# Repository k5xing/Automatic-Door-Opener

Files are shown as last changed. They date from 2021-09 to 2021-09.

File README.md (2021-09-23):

# Automatic-Door-Opener
Lab Projects Developed in ECE298

This project automates an entry/exit doorway to a customer site that senses customers automatically with programmable trigger levels for proximity. There are four labs to finish the project. The work done in each lab is described below and in the reports. Some detailed information of this project can be seen on Page 8 of [project overview.pdf](https://github.com/k5xing/Project-Overview/blob/main/project%20overview%20-%20Kehan%20Xing.pdf), and the code programmed in Lab3 is in [STM32_Workspace/Lab3/Core/Src/main.c](https://github.com/k5xing/Automatic-Door-Opener/blob/main/Lab3%20%20-%20Prototype%20Phase%201/STM32_Workspace/Lab3/Core/Src/main.c).

### Lab1 - Feasibility Model Phase 1
	• Design and pick sensors, actuators, and user I/O the project requires
	• Implement component tests in Proteus 

### Lab2 - Feasibility Model Phase 2
	• Design voltage translation interfacing

### Lab3 - Prototype Phase 1
	• Upgrade design to include all component models and connections
	• Program embedded MCU code and test functionalities

### Lab4 - Prototype Phase 2
	• Design a Printed Circuit Board (PCB) Layout

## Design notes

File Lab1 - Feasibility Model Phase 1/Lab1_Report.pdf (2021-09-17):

# Lab 1 – Feasibility Model Phase 1

ECE 298 – S2021

Team Members Kehan Xing (k5xing@uwaterloo.ca) Yiru Wu (y645wu@uwaterloo.ca)

Team Number 50

## Part 1 – Project Design Requirements

### 1. Functional Requirements

A. Automatically open the doorway to 8 feet wide when detecting a customer
B. Stop the door movement within 0.2 seconds after the collision switch is closed
C. Limit the door speed to 0.5 ft/sec when the collision switch opens again until the door is closed

### 2. Non-functional Requirements

A. Safety: The automatic door needs to ensure the safety of users during use.
B. Power efficiency: The automatic door needs to ensure the power effect and reduces losses.
C. Durability: The automatic door needs to guarantee the quality of use within a certain period of time.

### 3. Constraint Requirements

A. Maximum cost of $150 to develop the project
B. Maximum weight of 2 kg for the hardware components
C. Maximum PCB size of 9cm x 15cm

## Part 2 – Project Considerations for I/O

### Project Sensors and User Inputs

- Outside/inside Distance Proximity Sensor: The sensor will react to the trigger and

output the reaction pulse signal, we could use an opamp to scale the sensor reaction

pulse signal into the MCU digital input range.

- Door Position Limit Switches(2): The output of the switch can be regarded as the

presence or absence of current, so we could use a signal converter to transform the

current into a voltage range for the MCU, and then use the internal ADC to get the

digital input.

- Motor Sensor: The motor sensor will output continuous digital signals, so we could

use an opamp to scale the pulse signal output into the MCU digital input range.

- Collision Switch: The output of the switch can be regarded as the presence or

absence of current, so we could use a signal converter to transform the current into

a voltage range for the MCU, and then use the internal ADC to get the digital input

- Keypad: The pins on the MCU will receive a voltage input when a key is pressed, so

we use an opamp to scale the keypad output voltage to the MCU input pin voltage

range, and then use the ADC to convert the input to digital input.

### Project Actuators and User Outputs

- LCD Display: Use MCU’s parallel interface to input signals to display characters.
- LED (4): Use a transistor so the MCU can switch the high-current device on and off.
- Door Motor: Use the internal PWM to control the motor
- Motor Controller IC: Use the MCU’s serial interface to control a motor controller IC.

### Project MCU Internal Resources

a. Internal Resources
- ADC: The ADC will be used to convert Analog input to Digital input. For example, the

input we receive from a switch will be a voltage of 0V or 3.3V, and the ADC will

convert it to 0 or 1.

- Interrupt: The motor needs to be stopped once the collision switch or the door

position limit switch is closed, and that requires an interrupt module to handle.

- GPIO: As we listed above, there are many user inputs and outputs as well as sensors

and actuators in this project. They need GPIO functions to read or write.

- Timer: With the timer and the motor sensor, we can calculate the speed and the

acceleration of the motor.

- PWM: Pulse-width modulation is needed to control the motor.
b. Software parameters
- Duration: We need a parameter to read the timer and use it to calculate speed and

acceleration.

- Conversion factor: There could be many conversion factors, such as conversion

between different distance units.

- Sensor status: We need parameters to read sensor status and use the signals we

receive to control the motor.

- Motorcycle: There should be a counter to track how many cycles the motor has

spinned in order to calculate the distance.

- Keypad input: Keypad inputs including selected mode and parameters in the setup

mode need software parameters to read them.

## Part 3 – Device Testing Methodology

### Device 1 – ECE_GEN_PBUTTON (Switch)

We chose this pushbutton switch to represent the Door Position Limit switches and the Collision Switch. To test the switch, a 3.3V input voltage and a voltage scope are used. One end of the switch is connected to the input voltage, and the other end is connected to the scope. We expect to see the scope show 3.3V when the switch is closed and show 0V when it’s open. The schematic in Figures 1&2 with a pull-down resistor R shows our idea.

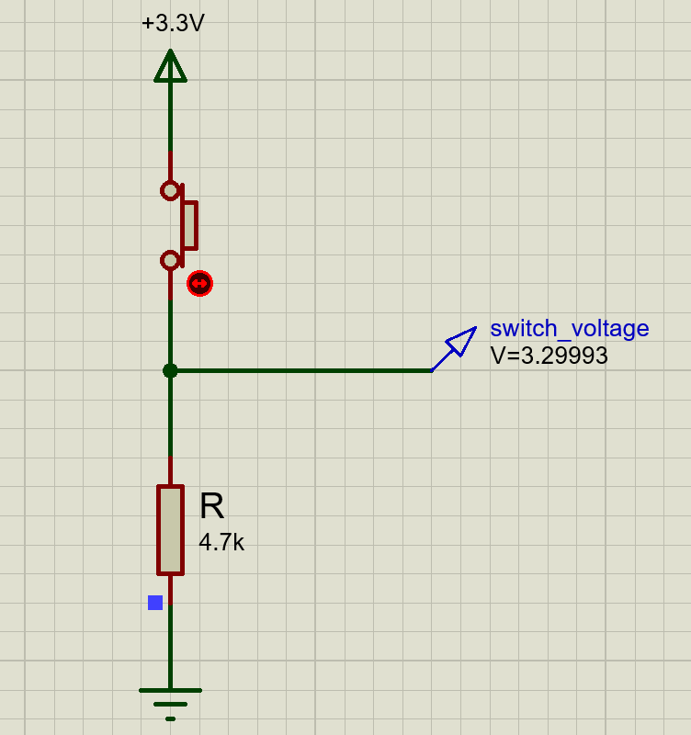
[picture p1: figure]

Figure 1: The schematic of ECE_GEN_PBUTTON -- Switch closed

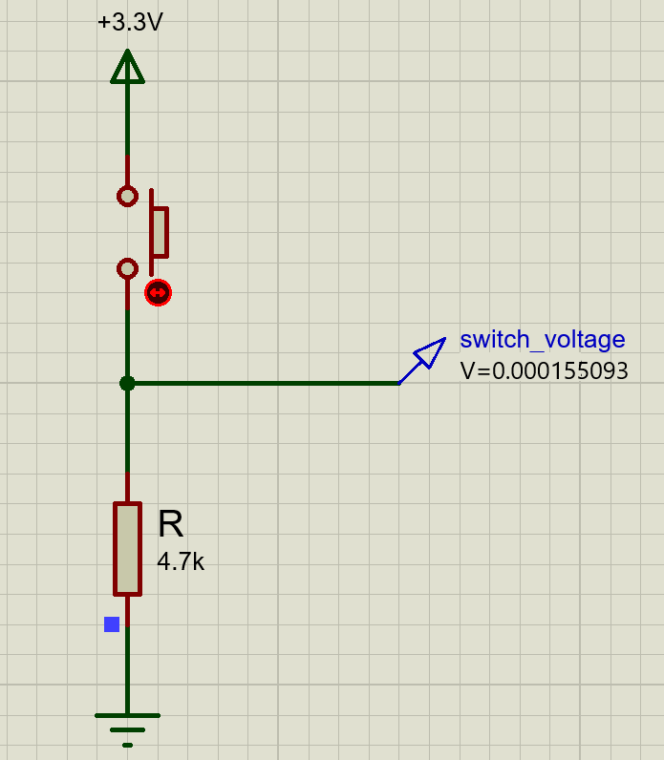
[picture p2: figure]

Figure 2: The schematic of ECE_GEN_PBUTTON -- Switch open

Verification: The switch works as expected. When the switch is closed, the voltage scope named switch_voltage shows a voltage value very close to 3.3V. Also, when the switch is open, the voltage scope shows a value close to 0V. This means the logic level is high when the switch is closed and is low when the switch is open.

Validation: As claimed in the verification section, a voltage of 5V indicates a high logic level, and a voltage of 0V indicates a low logic level. When using the switch in our project, we want the voltage scope to be replaced by an input pin on the MCU. In this case, the pin will read a high state when the switch is closed and a low state when the switch is open with the internal ADC, so this will work properly in our project.

### Device 2 – HCSR04 (Distance Proximity Sensor)

This ultrasonic ranging module is chosen for the Outside/Inside Distance Proximity Sensors. To test this sensor, we used a pulse voltage for its trigger input and an oscilloscope to show the trigger input and receive the echo pulse output. We expect to see both the signals on the oscilloscope.

Figure 3 and Figure 4 show the schematic and the signal displayed by the oscilloscope with distance = 50cm, and Figure 5 and 6 show those with distance = 200cm.

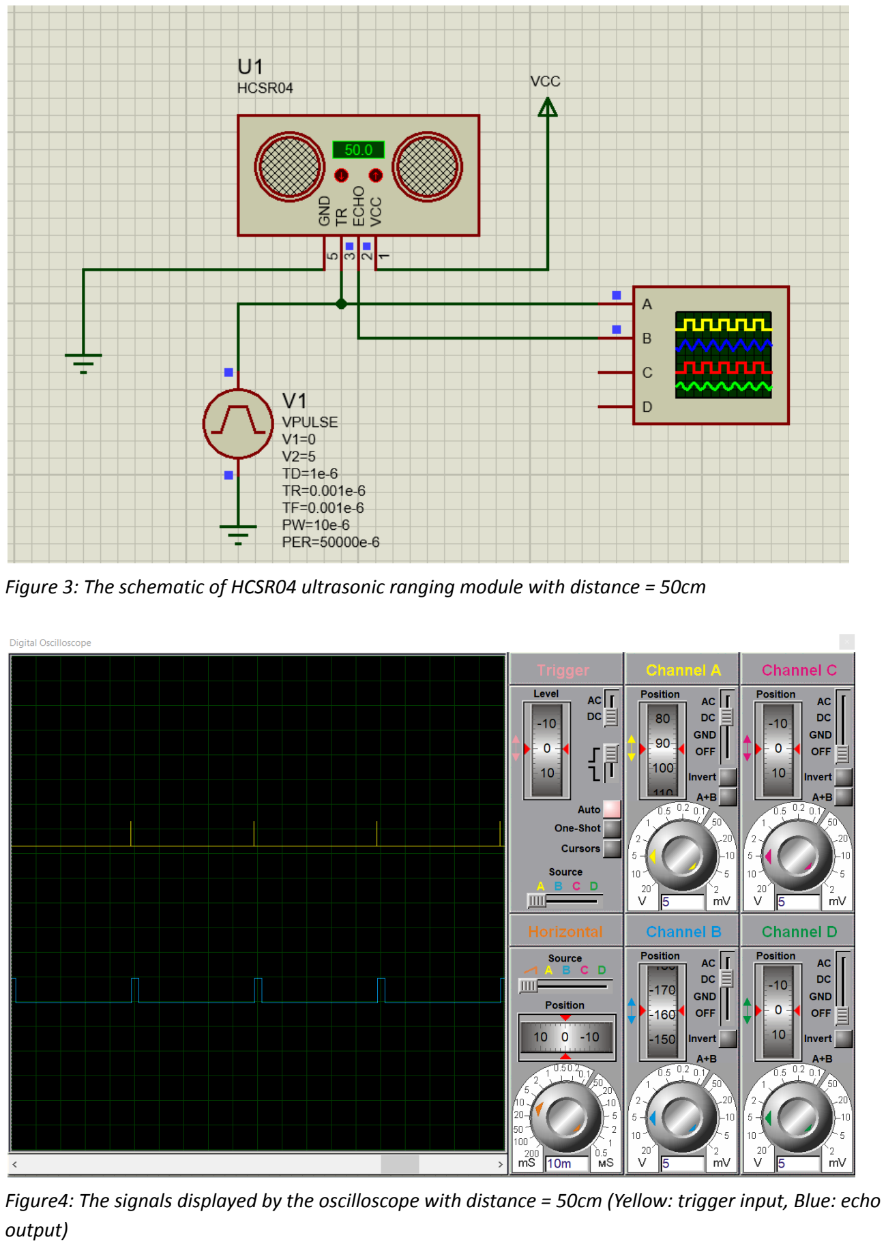
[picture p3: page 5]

Figure 3: The schematic of HCSR04 ultrasonic ranging module with distance = 50cm

Figure4: The signals displayed by the oscilloscope with distance = 50cm (Yellow: trigger input, Blue: echo output)

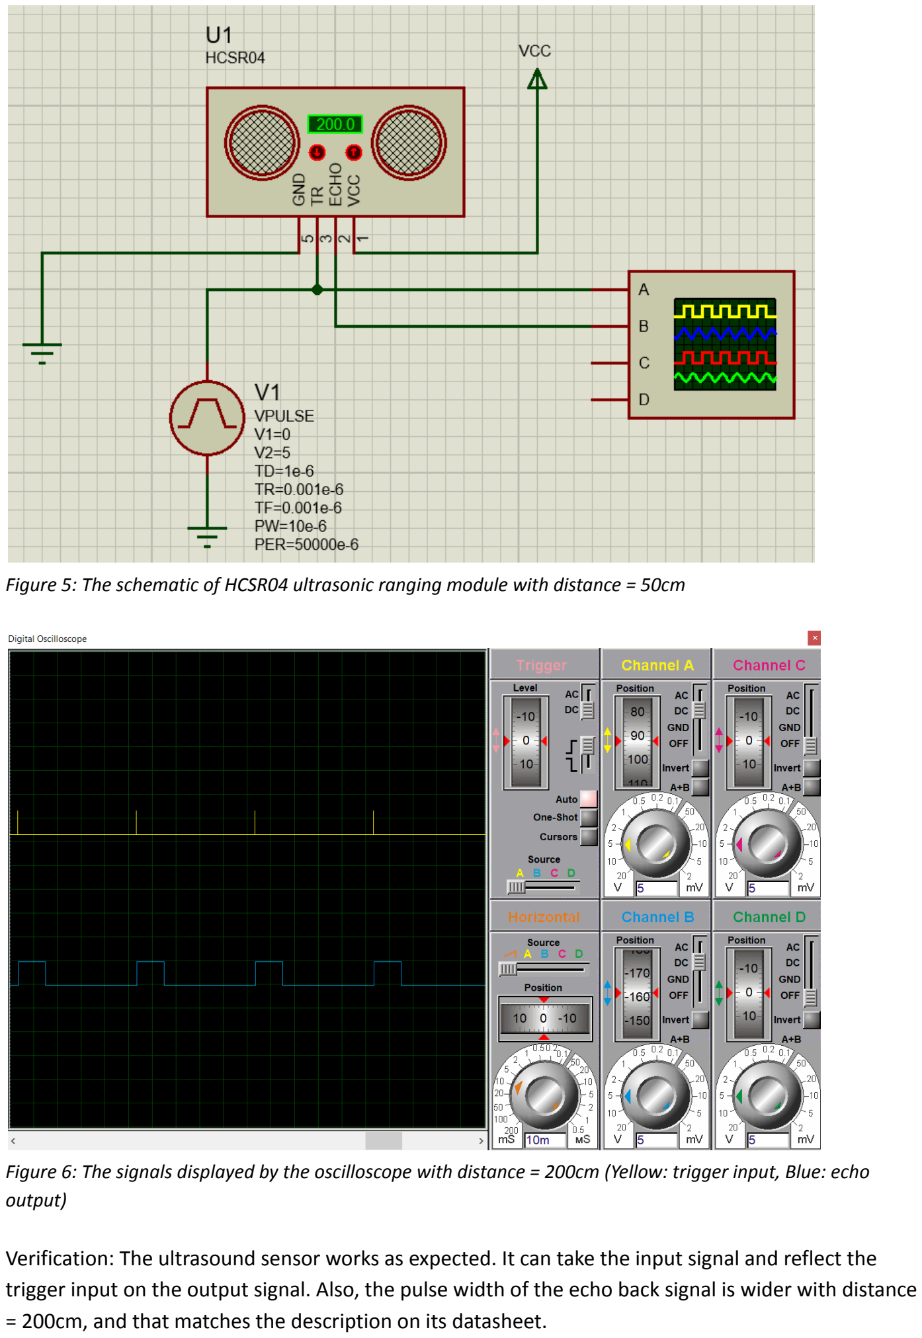
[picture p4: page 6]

Figure 5: The schematic of HCSR04 ultrasonic ranging module with distance = 50cm

Figure 6: The signals displayed by the oscilloscope with distance = 200cm (Yellow: trigger input, Blue: echo output)

Verification: The ultrasound sensor works as expected. It can take the input signal and reflect the trigger input on the output signal. Also, the pulse width of the echo back signal is wider with distance = 200cm, and that matches the description on its datasheet.

Validation: The ultrasonic sensor is used to measure the distance of a target object by emitting ultrasonic sound waves, and converts the reflected sound into an electrical signal. This is exactly the functionality we want for the distance proximity sensor. Also, the detecting range of this ultrasonic ranging module is 2cm - 500cm, and the required range of our project is 60cm - 240cm. Therefore, this ultrasonic sensor can be used in our project.

### Device 3 – KEYPAD - PHONE (Keypad)

The keypad - phone is chosen to be used in Setup Mode. To test this keypad, we selected four DC power supplies each providing different voltage. Then using three DC voltmeters to test the voltage changes when the keys were pushed. Figure 7, figure 8, figure 9 and figure 10 show the schematic and the voltage change.

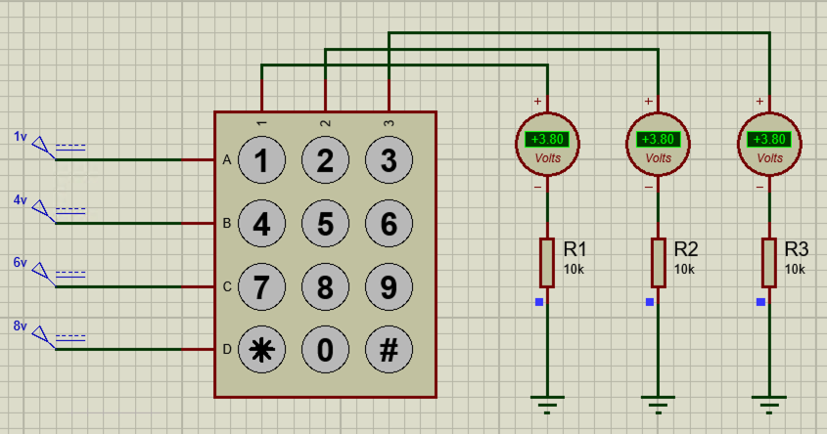
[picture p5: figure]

Figure 7: The schematic of KEYPAD module (initial state)

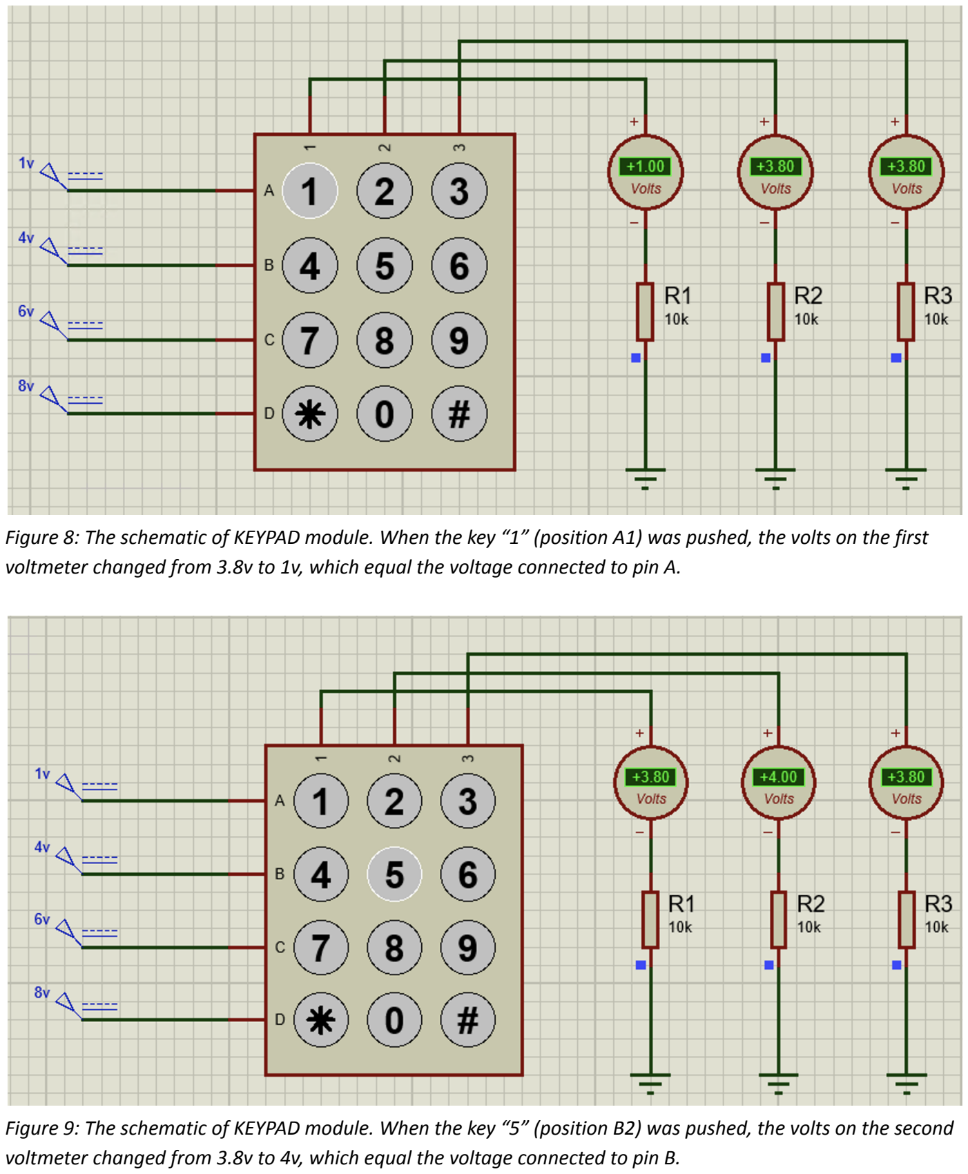
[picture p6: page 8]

Figure 8: The schematic of KEYPAD module. When the key “1” (position A1) was pushed, the volts on the first voltmeter changed from 3.8v to 1v, which equal the voltage connected to pin A.

Figure 9: The schematic of KEYPAD module. When the key “5” (position B2) was pushed, the volts on the second voltmeter changed from 3.8v to 4v, which equal the voltage connected to pin B.

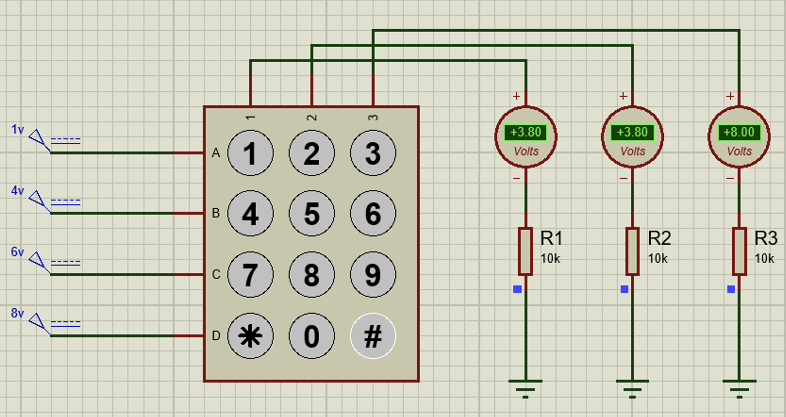
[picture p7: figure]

Figure 10: The schematic of KEYPAD module. When the key “#” (position D3) was pushed, the volts on the third voltmeter changed from 3.8v to 8v, which equal the voltage connected to pin D.

Verification: The keypad works as expected. When the key located at (x,y) be pressed, the pin x and the pin y are connected, so the voltage of pin y equals the voltage of pin x, as measured by voltmeter. Detailed information of all the cases is described under the figures.

Validation: When using the keypad in our project, the total 7 pins of the keypad will be connected to the MCU. Then we could detect which key is pressed by checking which pins are connected. Also, the user input required in our project are just numbers, so this keypad can satisfy the requirement.

### Device 4 – ECE298_FAST_DCMOTOR_ENCODER (Motor/Motor Sensor)

This model is chosen to be used as motor and motor sensors. To test this motor, we need a DC voltage to supply the power and an oscilloscope to show the digital signal detected from the motor. Figure 11, figure 12 and figure 13 show the schematic and the signal displayed by the oscilloscope using a pulse voltage input. Figure 14, figure 15 and figure 16 shows that using a DC voltage.

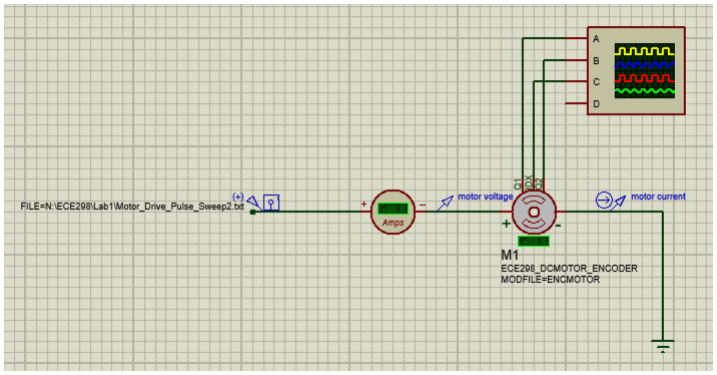
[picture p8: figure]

Figure 11: The schematic of ECE298_FAST_DCMOTOR_ENCODER using pulse voltage

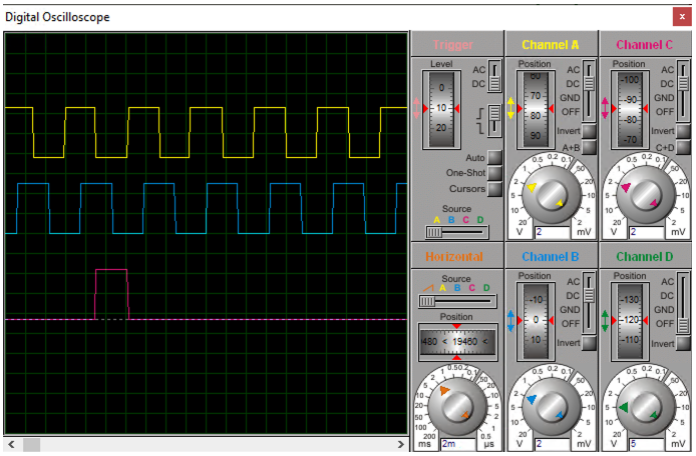
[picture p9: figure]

Figure 12: The signals output displayed by the oscilloscope using pulse voltage(Yellow: Q1, Blue: Q2, Red: IDX)

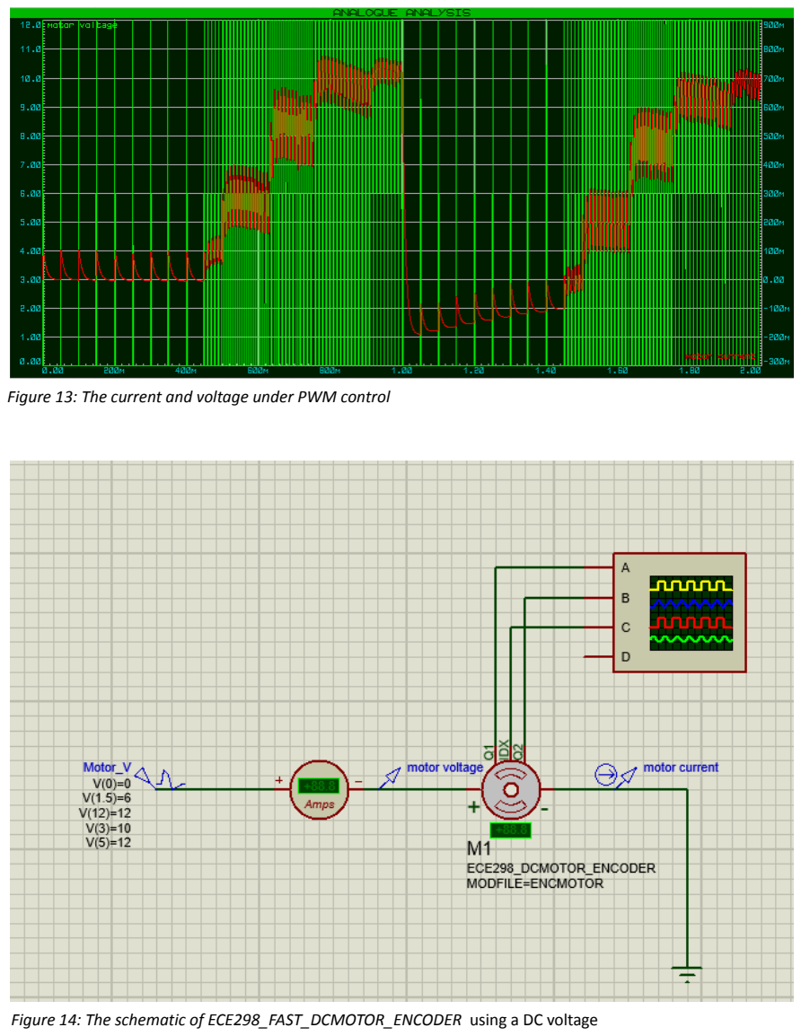
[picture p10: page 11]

Figure 13: The current and voltage under PWM control

Figure 14: The schematic of ECE298_FAST_DCMOTOR_ENCODER using a DC voltage

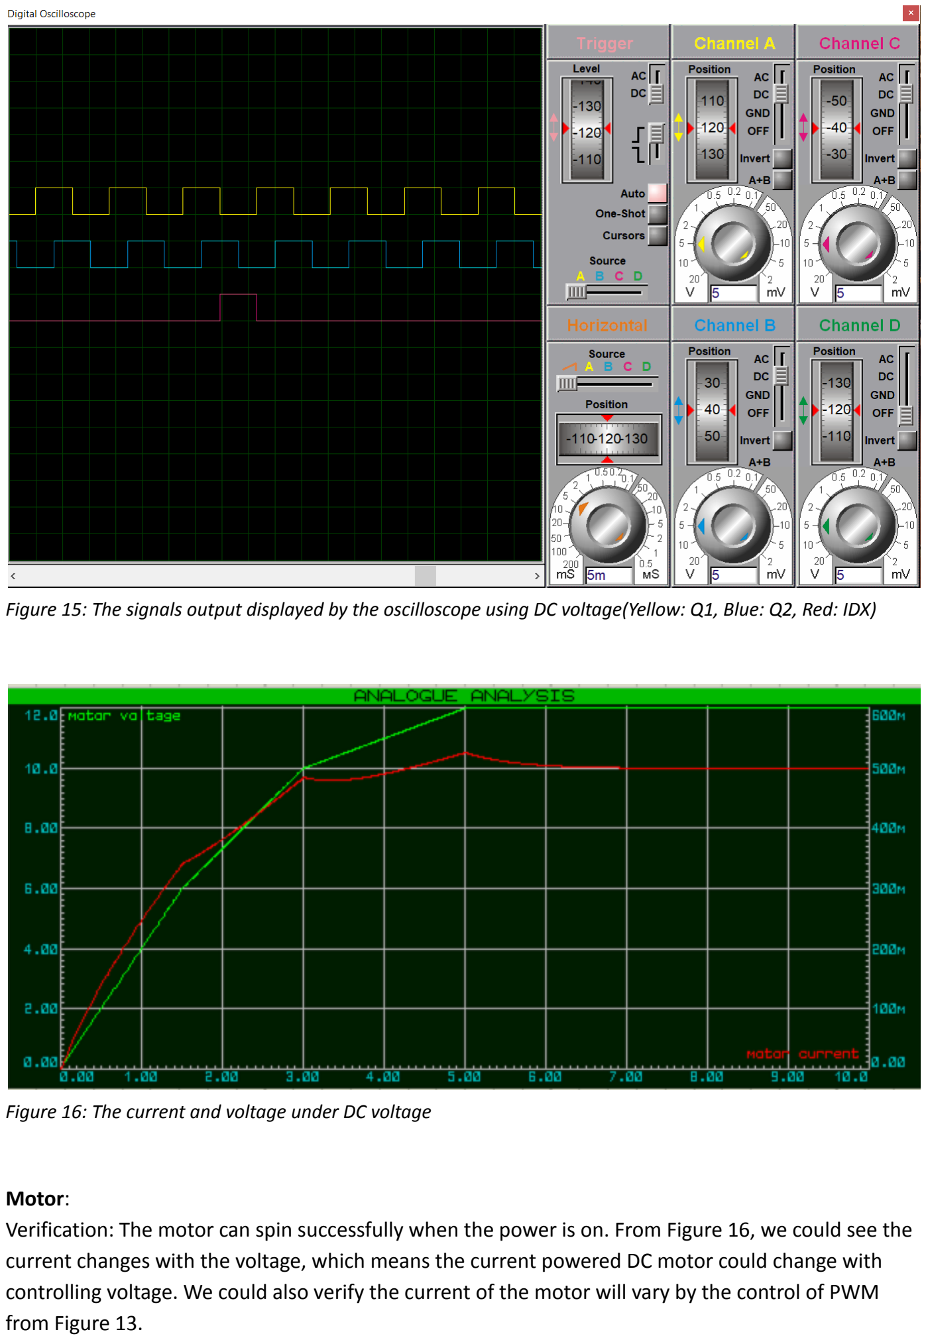
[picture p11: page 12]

Figure 15: The signals output displayed by the oscilloscope using DC voltage(Yellow: Q1, Blue: Q2, Red: IDX)

Figure 16: The current and voltage under DC voltage

Motor:
Verification: The motor can spin successfully when the power is on. From Figure 16, we could see the current changes with the voltage, which means the current powered DC motor could change with controlling voltage. We could also verify the current of the motor will vary by the control of PWM from Figure 13.

Validation: This motor is a good choice for us because it has a sensor attached. It can also spin properly. In the project, we are able to change the speed of the motor by controlling the PWM and make the motor rotate in the opposite direction by reversing power.

Motor Sensor:
Verification: From the graph generated by the oscilloscope, we could see the digital signals from the pins of the motor, so the motor sensor is working properly to record the move of the sensor.

Validation: In the project, we could use the digital signals from Q1 and Q2 to determine the direction of the motor. Also, we could use an internal counter to record the number of edges of the digital signal as revolutions of the motor.

### Device 5 – LED (LED)

Three kinds of LEDs are used in this project, and we decided to use animated LED models with different colors to represent them. These LEDs have a forward voltage of 1.95V(red), 2V(yellow) and 2.1V(green) according to the information on Piazza. And they all have a full drive current of 10mA, so we calculated the resistances of their current limiting resistors based on those values and MCU voltage of 3.3V and created a schematic.

R =

V−V
led
I
led

The schematic also used a potentiometer to change the current flows through the LEDs. After changing the LED model type to analog, the brightness of the LEDs should change with the current. The figures below show the brightness with current of approximately 100%, 50% and 20% of the full drive current.

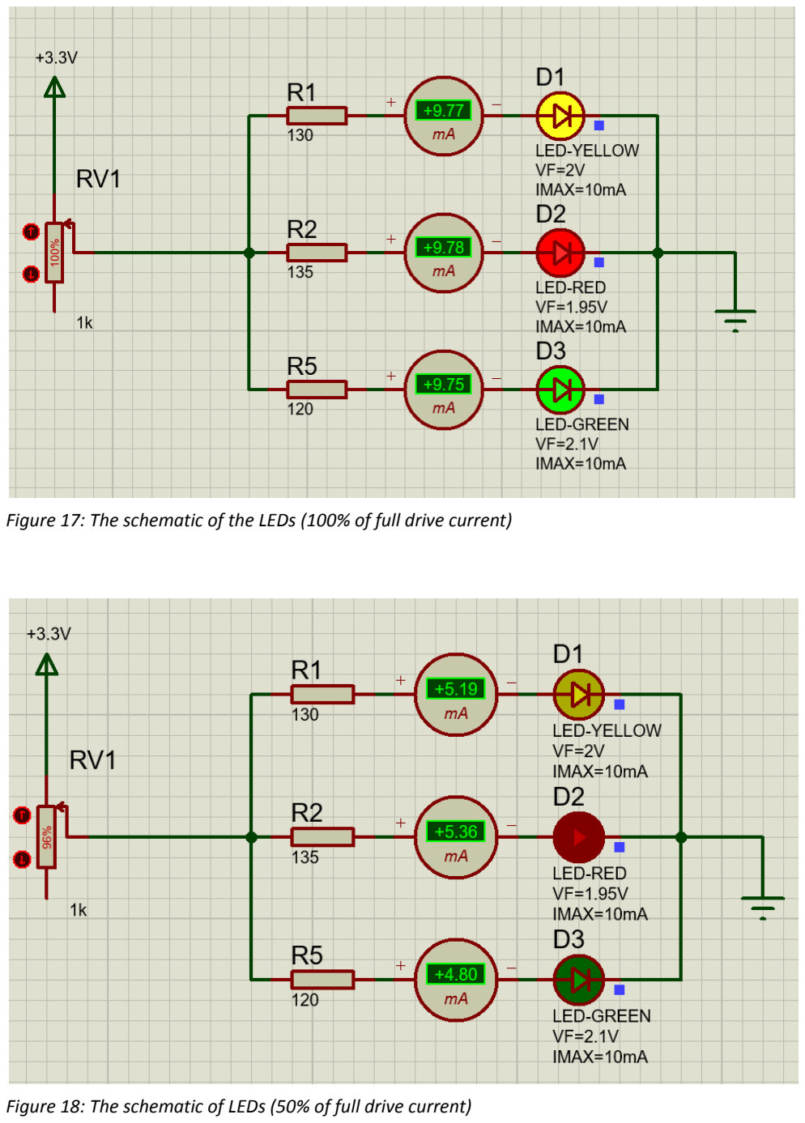
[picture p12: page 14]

Figure 17: The schematic of the LEDs (100% of full drive current)

Figure 18: The schematic of LEDs (50% of full drive current)

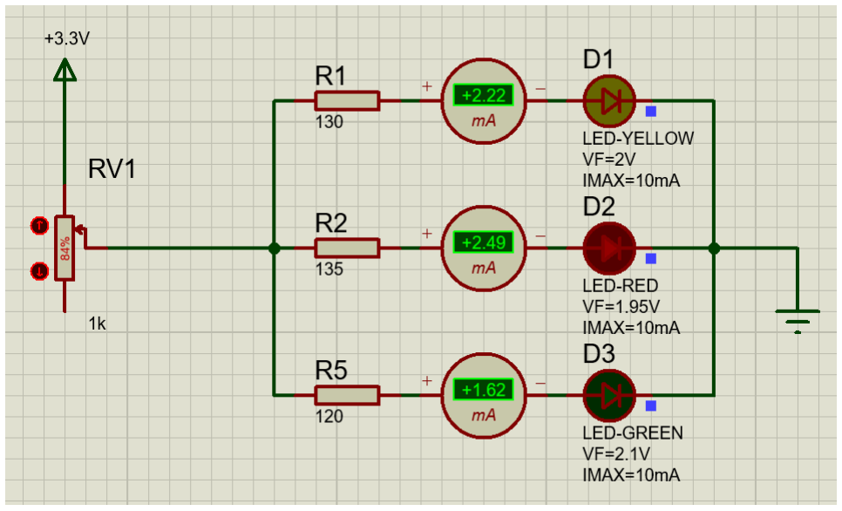
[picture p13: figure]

Figure 19: The schematic of LEDs (20% of full drive current)

Verification: The LEDs worked as expected. They can be turned on after powering the circuit, and the brightness of the LEDs changes with the current flow through them. We also confirmed the current-limiting resistors for these LEDs are calculated correctly because the ammeter displayed a value very close to 10mA when the potentiometer is not used in Figure 16.

Validation: These LEDs have a forward voltage of 1.95V, 2V and 2.1V, and our voltage source in this project will be 3.3V, so the LEDs can perform normally as shown above. For the project requirements, we only require a LED to turn on when a specific event happens. This can be achieved by addressing a high state to the pin to power the LED.

### Device 6 – LM016L– (LCD display)

We chose this LCD for our project because it is simple to use and can display letters as well as numbers. To test this device, we connect the pattern generator to the LCD like Figure 20, and change the pattern to display our group number.

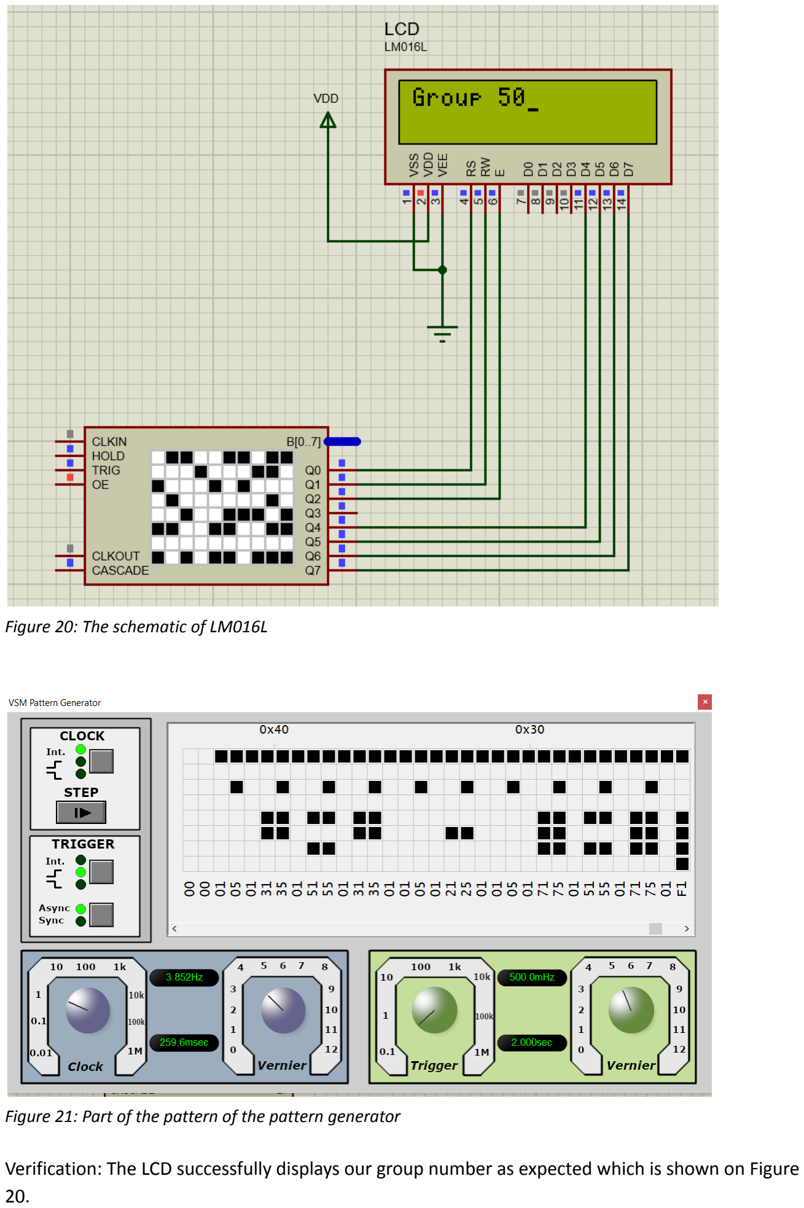
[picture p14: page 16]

Figure 20: The schematic of LM016L

Figure 21: Part of the pattern of the pattern generator

Verification: The LCD successfully displays our group number as expected which is shown on Figure 20.

Validation: In our project, we want to display mode, parameter name and parameter value. They will be either letters or numbers. We tested that both of them can be displayed successfully on this LCD, so we can use the LCD in our project.

## Part 4 – System-Level Design

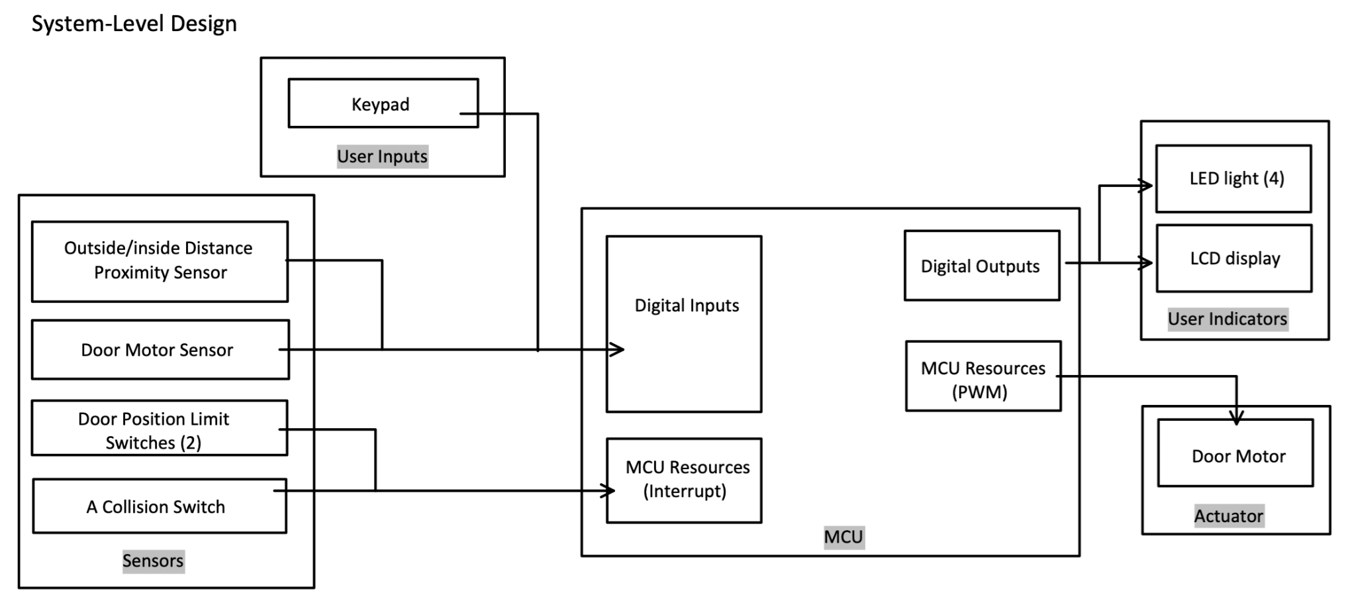
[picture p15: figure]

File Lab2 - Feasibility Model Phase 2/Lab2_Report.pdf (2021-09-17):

# Lab 2 – Feasibility Model Phase 2

ECE 298 – S2021
Lab Section: | Group: | 50

## {Switch}

### Summary

Item | Description

Purpose

A switch is required to represent the collision switch and the door position limit switches, so it will stop the door movement when a collision occurs, or the door reaches its limit position.
Device physical domain and range | The physical domain and range are not applied to this device.
Device type chosen | The chosen switch is an on/off type.
Proteus Library component name | There is no direct Proteus push button component directly
available, so ECE_GEN_PBUTTON is used in its place.
Device input / output properties | The device outputs a digital output. The type of the digital
output is push/pull, but it requires a pull-down resistor.
Device input / output range | The input/out range is not applied to this device.
MCU connectivity details | The device will connect to an MCU digital input.
Device/MCU interfacing details | There is no interface provided for the switch because it can be
connected to a 3.3V power directly.

### Schematics and Simulations


Figure 2.1.1 The schematic of ECE_GEN_PBUTTON -- Switch closed

Lab 2 – Feasibility Model Phase 2


ECE 298 S2021 | Page 2 of 13

Figure 2.1.2: The schematic of ECE_GEN_PBUTTON -- Switch open

The schematic used for the switch is same as Lab1 because the switch can connect to a 3.3V power directly without voltage translation. The switch_voltage probe represents an MCU digital input. The probe shows 3.3V when the switch is closed and shows 0V when it is open.

## {Distance Proximity Sensor}

### Summary

Item | Description
Purpose | The distance proximity sensors are required to detect people
| and objects near the door from both directions.
Device physical domain and range | The distance range that the chosen distance proximity sensor
| support is 2cm - 500cm.
Device type chosen | The chosen distance sensor is an ultrasonic ranging module.
Proteus Library component name | HCSR04
Device input / output properties | The device receives a digital input as trigger signal and outputs
| the echo back signal which is a digital output.
Device input / output range | The device requires a digital active-high trigger signal and
| outputs a variable pulse width echo signal. The recommended
| cycle period is less than 50ms, and the echo pulse width is
| proportional to the measured distance. Other information such
| as maximum/minimum pulse width and VOH/ VOL / VIH / VIL is not
| available.
MCU connectivity details | The device uses an MCU digital output for the trigger input, and
| an MCU digital input for the echo signal.
Device/MCU interfacing details | The interfaces used are digital-to-digital. The first interface
| translates the 3.3V digital input from the MCU to a 5V digital
| input and pass it to trigger signal. The second interface translate
| the 5V digital output from the echo signal translate to a 3.3V
| digital output and pass it to an MCU digital input pin.

### Schematics and Simulations

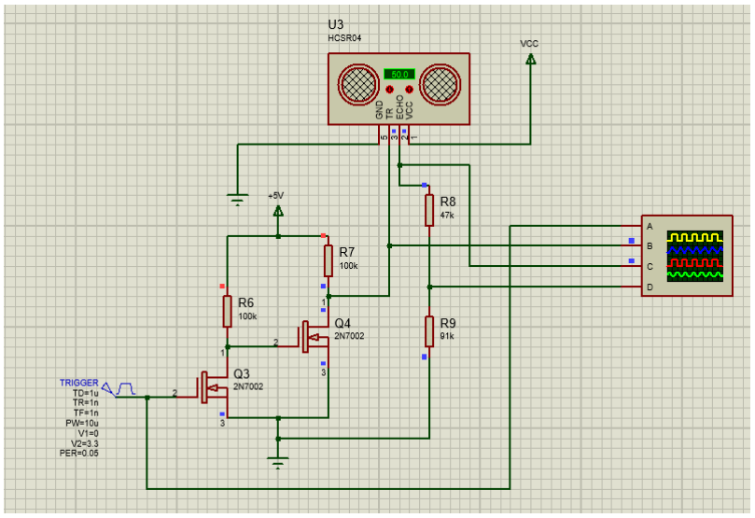
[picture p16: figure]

Figure 2.2.1: The schematic of HCSR04 ultrasonic ranging module with distance = 50cm

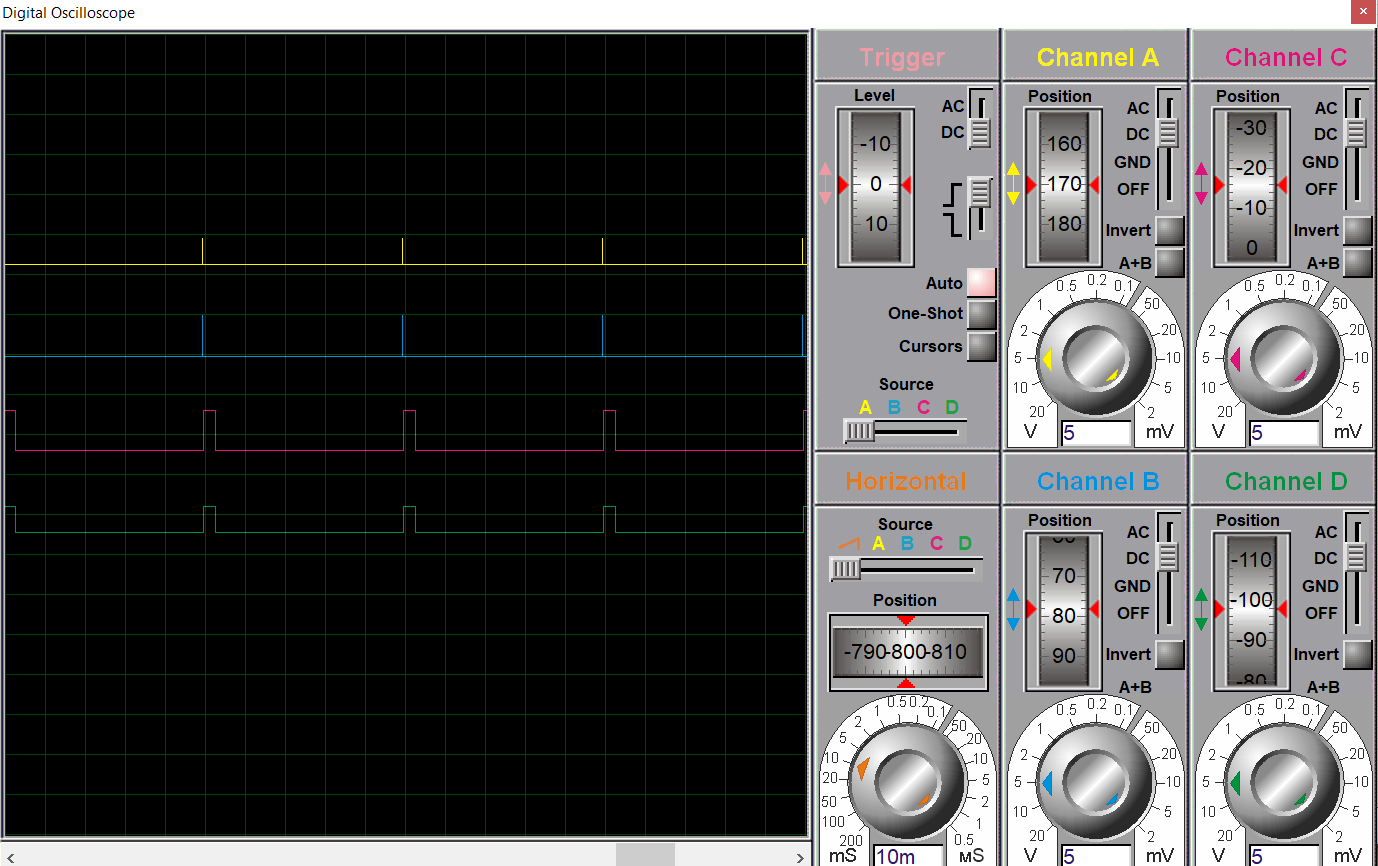
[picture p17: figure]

Figure 2.2.2 The signals displayed by the oscilloscope with distance = 50cm (Yellow: original MCU input, Blue: trigger input after translation, Pink: original echo output, Green: echo output after translation)

As described in the summary table, a step-up interface and a step-down interface are used in the schematic. The step-up interface uses two N-FET and translates the 3.3V digital input from the MCU to a 5V digital input and pass it to trigger signal. Channel A of the oscilloscope shows the original 3.3V input from MCU, and channel B shows the digital input after translation. The step-down interface uses two resistors with resistance 47k and 91k and translates the 5V digital output from the echo signal translate to a 3.3V digital output. Channel C shows the 5V digital output, and Channel D shows the signal after translation. The signal displayed in Channel D is the output that will be passed to an MCU digital input.

## {Keypad}

### Summary

Item | Description
Purpose | A keypad is required to select mode of operation and input
| parameter values.
Device physical domain and range | The keypad is an array of switches, so the physical domain and
| range are not applied to it.
Device type chosen | The keypad is an array of switches, and the switches are on/off
| type. When a key is pressed, the corresponding switch is closed;
| when a key is not pressed, the corresponding switch is open.
Proteus Library component name | KEYPAD - PHONE
Device input / output properties | The device receives three digital inputs for pins representing
| columns and outputs four digital outputs from pins representing
| rows. The type of the digital output is push/pull, but it requires
| a pull-down resistor.
Device input / output range | The keypad is an array of switches, so the input/out range is not
| applied to this device.
MCU connectivity details | The device uses three MCU digital outputs connecting to pins
| representing columns and four MCU digital inputs for pins
| representing rows.
Device/MCU interfacing details | The keypad is an array of switches, so there is no interface
| provided for the switch because it can be connected to a 3.3V
| digital signal directly.

### Schematics and Simulations

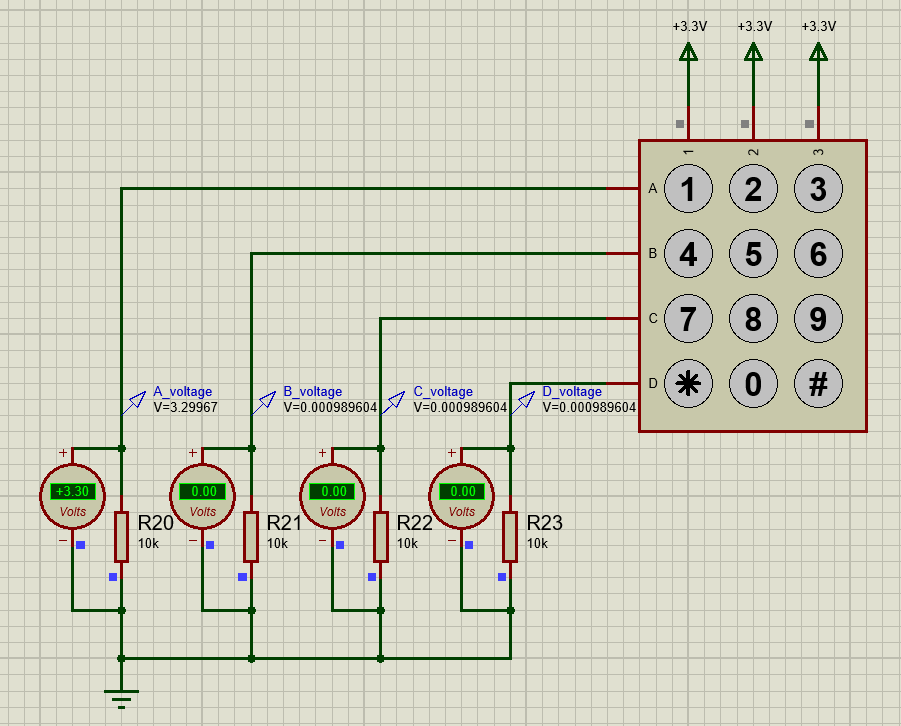
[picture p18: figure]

Figure 2.3.1: The schematic of KEYPAD_PHONE when key ‘1’ is pressed

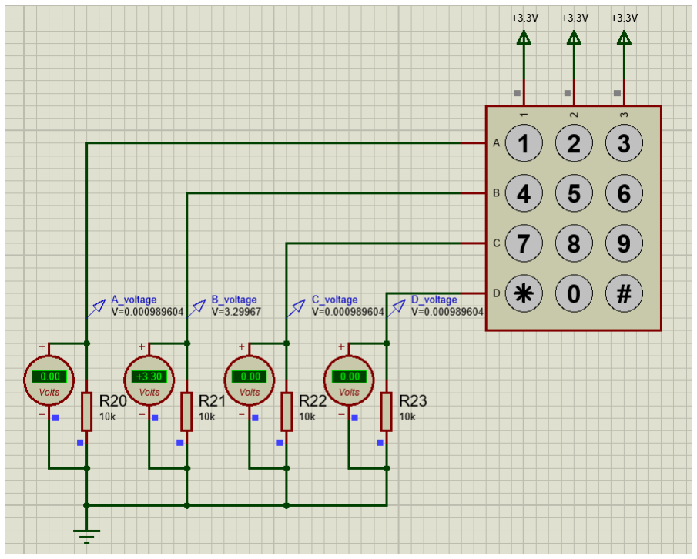
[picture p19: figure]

Figure 2.3.2: The schematic of KEYPAD_PHONE when key ‘5’ is pressed

The keypad doesn’t require voltage translations because it’s simply an array of switches. The two figures above show the schematic when the key ‘1’ and ‘5’ is pressed, and it shows that the voltage of the corresponding pin turns to 3.3V when the key is pressed. The 3.3 voltage power represents the digital signal of ‘1’ receiving from MCU digital output, and the probes labeled A_voltage, B_voltage, C_voltage, D_voltage represent the signal will be passed to MCU digital inputs.

## {LED}

### Summary

Item | Description
Purpose | Different color of LEDs are used to indicate different status of
| door motor.
Device physical domain and range | LED’s maximum brightness will depend on the specific LED.
Device type chosen | Normal LED
Proteus Library component name | LED-RED, LED_GREEN, LED_YELLOW
Device input / output properties | The device will receive the digital signal from MCU as digital
| input.
Device input / output range | We setup the current through LED to be 10mA.
MCU connectivity details | The LED will use an MCU digital output for the trigger signal.
Device/MCU interfacing details | The interface is digital to digital, if MCU inputs a ‘1’ (3.3v), the
| circuit of LED will connect to 5v voltage source and groud to
| generate a 10mA current for LED to work, the LED will light up;
| if MCU inputs a ‘0’ (0v), the LED will not light up.

### Schematics and Simulations

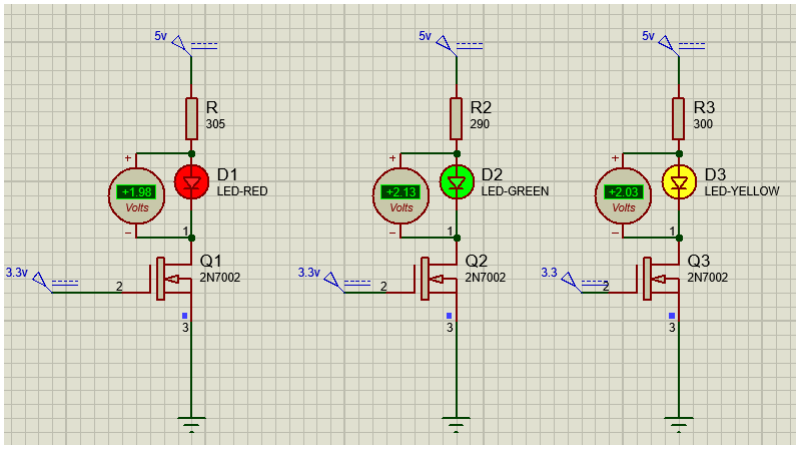
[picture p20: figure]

Figure 2.4: Schematics of converting digital input to voltage range for LEDs. To step up the voltage to the input range of LED, we add a N-FET. The #1 pin connects to the 5v and LED, #2 pin connects to the digital output of MCU, and #3 connects to ground. When MCU outputs a ‘0’, which means that V2 = 0v and V23 = 0v, then circuit between #1 pin and #3 pin is open circuit, the led would not work well. When MCU outputs a ‘1’, which means that V2=3.3v and V23=3.3v, then #1 pin and #3 pin is connected, and there is a 10mA current through the LED to support.

Through the Lab1 piazza, we knew that LEDs with different colors have different work voltage: 1.95v for red LED, 2v for yellow LED, and 2.1v for green LEDs. The current for LEDs to work is 10mA. The resistance connect to LED should be 5v-V(work)/I(work). Therefore, the resistance for red LED is 305 ohm, for yellow LED is 300 ohm, and for green LED is 290 ohm.

## {LCD}

### Summary

Item | Description
Purpose | LCD is used to indicate the Mode, Parameter Name and
| Parameter Value in Setup Mode, and it is also used to display
| the status of the automatic door.
Device physical domain and range | Operating temperature should be 0 – 50 degrees.
Device type chosen | A character display LCD
Proteus Library component name | LM016L
Device input / output properties | The LCD will receive a digital input and convert it to characters
| by Ascii table to display required characters.
Device input / output range | The LCD accepts input range from 0v to 5v.
MCU connectivity details | LCD receives the digital outputs from MCU and converts the
| digital signal (which always present as ‘0’ or ‘1’) to the
| characters by Ascii table and display the received characters.
Device/MCU interfacing details | The interface is digital to digital, MCU will send a serial of digital
| signals and LCD receive and translate these signals.

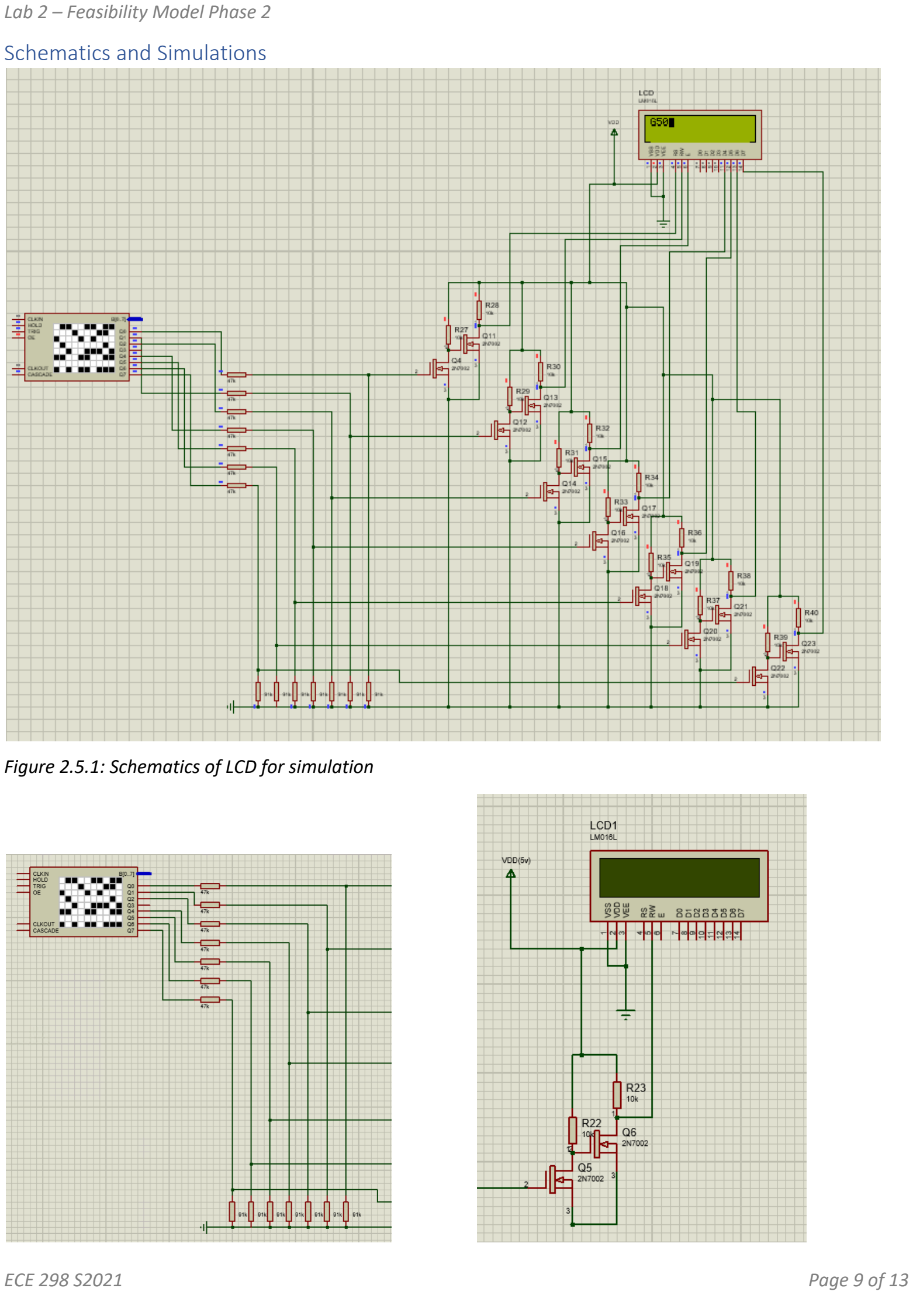
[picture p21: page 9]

### Schematics and Simulations

Figure 2.5.1: Schematics of LCD for simulation

Figure 2.5.2: Simulation the output signal of MCU Figure 2.5.3: Converting to LCD input range
We used the step-down voltage interface and generator to simulate the digital output of MCU as Figure 2.5.2. The schematics showed in Figure 2.5.2 is converting an 5v digital signal to 3.3v digital signal to simulate the actual MCU digital output.
To convert the digital signal to the range of LCD, we connected the circuit as Figure 2.5.3. Two N-FETs are used to convert the 3.3v digital to 5v. The left N-FET (Q5) connect to the 3.3 digital signal with #2 pin. When the
MCU output ‘1’ (3.3v), The voltage at #1 pin of Q4 N-FET is 0v, thus the circuit between Q6 N-FET's #1 and #2 pins are open circuit, then the voltage at #1 pin of Q6 is equal to VDD = 5v. If MCU output ‘0’ (0v), the circuit between #1 and #3 pins of Q5 is open circuit, and then #1 and #3 of Q6 is connected, so the voltage at #1 pin of Q6 is 0v.

## {Motor}

### Summary

Item | Description
Purpose | The Door Motor is used to open and close the door.
Device physical domain and range | The motor rpm is unknown, because the motor model we use
| does not have a specific datasheet. The rpm of most motors is 0
| to 800, we assume the same is true for the motor model we use
Device type chosen | Brushed DC Motor
Proteus Library component name | ECE298_DCMOTOR_ENCODER (Actuators)
Device input / output properties | The motor will receive analog voltage input.
Device input / output range | An analog DC motor accepts 0v to 12v.
MCU connectivity details | The MCU will output a digital signal to the motor driver, then
| the motor driver will convert the digital signal to PWM signal for
| motor.
Device/MCU interfacing details | For the MCU to motor driver part, it converts digital to analog
| by adding a VDD voltage and map the digital signal to PWM
| voltage to supply motor.

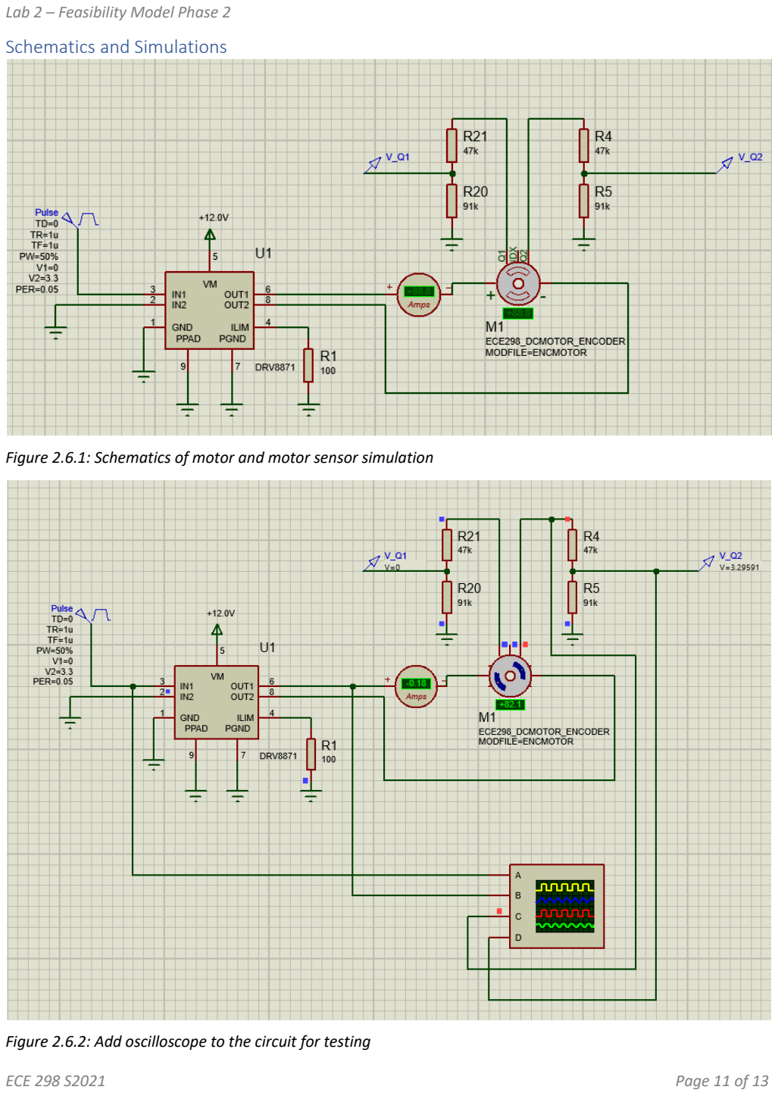
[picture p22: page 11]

### Schematics and Simulations

Figure 2.6.1: Schematics of motor and motor sensor simulation

Figure 2.6.2: Add oscilloscope to the circuit for testing

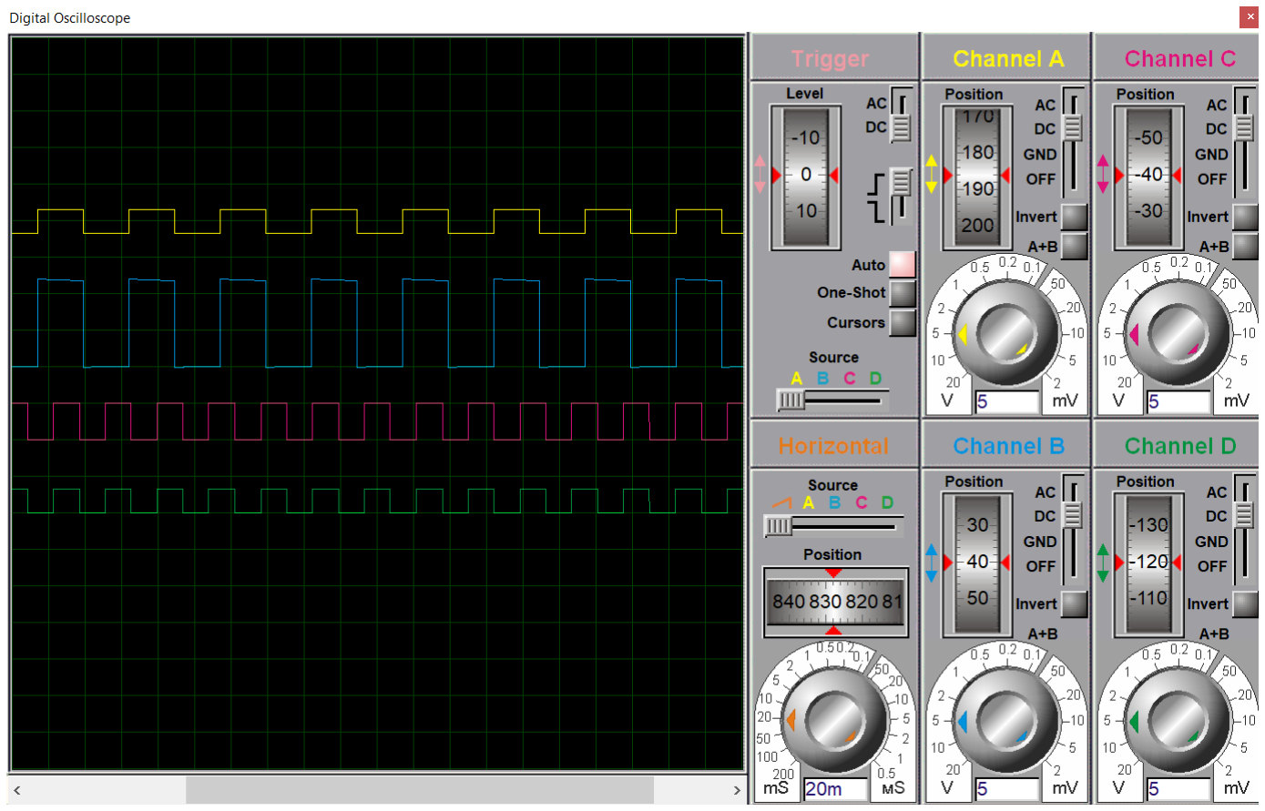
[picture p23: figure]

Figure 2.6.3: Display of oscilloscope.
We used the pulse source to simulate the digital output from MCU. The IN1 pin of motor driver connects to the digital signal, VM pin connect to motor work voltage 12v, OUT1 and OUT2 connect to the motor to supply voltage. The motor driver (DRV8871) converts the received digital signal to PWM within 0v to 12v. We could confirm the signal by oscilloscope, channel A shows the input digital signal from MCU (0 - 3.3v); channel B shows the output signal from motor driver to motor, we could see the height of wave is much higher, which means the voltage has step up to 0v – 12v for motor.

## {Motor Sensor}

### Summary

Item | Description
Purpose | Door motor sensor is used to monitor the door travel, including
| position, speed, and acceleration.
Device physical domain and range | The physical domain and range are not applied to this device.
Device type chosen | Internal motor encoder
Proteus Library component name | ECE298_DCMOTOR_ENCODER (Encoder)
Device input / output properties | The digital outputs of motor sensor are modelled as being TTL
| compatible.
Device input / output range | The output signal of motor sensor is 0v to 5v
MCU connectivity details | The motor sensor output a digital signal to MCU.
Device/MCU interfacing details | Hidden VCC of the encoder is 5v, we need to step down the
| voltage range to 0 – 3.3v for MCU input.

### Schematics and Simulations

The motor sensor is encoded by the motor, we could see the how the motor sensor works from schematic of motor.
The VCC of motor sensor is 5v, channel C shows the output signal from encoder, the range of this output is 0v-5v. Then we add step down voltage interface (one 47k ohm and one 91k ohm) to reduce the voltage range to 0v –3.3v to fit the input signal range of MCU. Oscilloscope’s Channel C and D shows the signal before step down and after, we could see the height of wave decreased. The point probe V_Q1 and V_Q2 located will connect to the MCU.

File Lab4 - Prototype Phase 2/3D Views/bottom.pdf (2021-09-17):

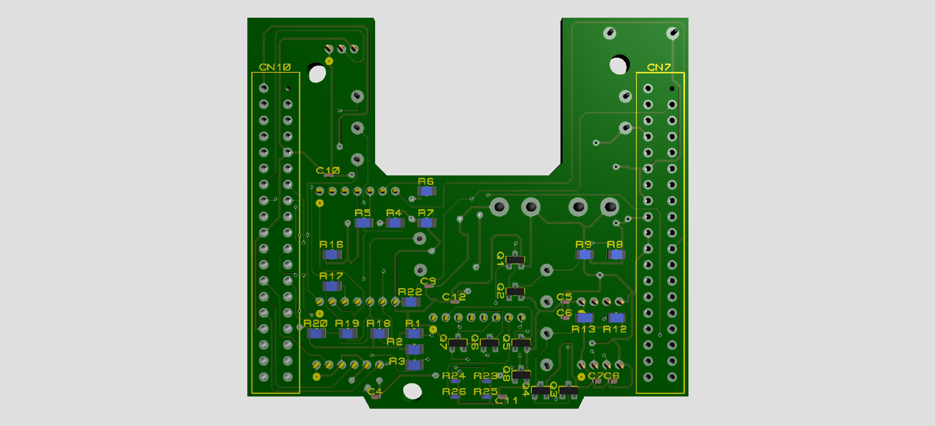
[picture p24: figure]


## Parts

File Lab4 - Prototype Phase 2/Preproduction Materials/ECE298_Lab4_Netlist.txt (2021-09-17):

ISIS SCHEMATIC DESCRIPTION FORMAT 8.0
=====================================
Design:   ECE298_Lab4.pdsprj
Doc. no.: <NONE>
Revision: <NONE>
Author:   <NONE>
Created:  2021-07-30
Modified: 2021-07-30

*PROPERTIES,0    

*MODELDEFS,0    

*PARTLIST,71   
C1,1206YD106KAT2A,10u,CODE="Digikey 478-1573-1-ND",EID=5,PACKAGE=CAPC3216X140
C2,1206YD106KAT2A,10u,CODE="Digikey 478-1573-1-ND",EID=7,PACKAGE=CAPC3216X140
C3,1206YD106KAT2A,10u,CODE="Digikey 478-1573-1-ND",EID=24,PACKAGE=CAPC3216X140
C4,04022F103Z7B20D,10000pF,CODE="Digikey 311-1045-2-ND",EID=21,PACKAGE=CAPC1005X55
C5,04022F103Z7B20D,10000pF,CODE="Digikey 311-1045-2-ND",EID=1A,PACKAGE=CAPC1005X55
C6,04022F103Z7B20D,10000pF,CODE="Digikey 311-1045-2-ND",EID=1B,PACKAGE=CAPC1005X55
C7,04022F103Z7B20D,10000pF,CODE="Digikey 311-1045-2-ND",EID=1E,PACKAGE=CAPC1005X55
C8,04022F103Z7B20D,10000pF,CODE="Digikey 311-1045-2-ND",EID=1F,PACKAGE=CAPC1005X55
C9,04022F103Z7B20D,10000pF,CODE="Digikey 311-1045-2-ND",EID=2A,PACKAGE=CAPC1005X55
C10,04022F103Z7B20D,10000pF,CODE="Digikey 311-1045-2-ND",EID=41,PACKAGE=CAPC1005X55
C11,04022F103Z7B20D,10000pF,CODE="Digikey 311-1045-2-ND",EID=C,PACKAGE=CAPC1005X55
C12,04022F103Z7B20D,10000pF,CODE="Digikey 311-1045-2-ND",EID=44,PACKAGE=CAPC1005X55
CN7,1-534236-9,1-534236-9,CODE=1-534236-9,EID=1,PACKAGE=ECE298_REVTRANS38DIL-1,SUPPLIER=TE_CONNECTIVITY
CN10,1-534236-9,1-534236-9,CODE=1-534236-9,EID=2,PACKAGE=ECE298_REVTRANS38DIL-1,SUPPLIER=TE_CONNECTIVITY
J1,TBLOCK-M2,TBLOCK-M2,EID=23,PACKAGE=TBLOCK-M2
J2,25630601RP2,25630601RP2,CODE="NorComp 25630601RP2",EID=13,PACKAGE=CON6_1X6_U_2563
J3,25630701RP2,25630701RP2,CODE="NorComp 25630701RP2",EID=3,PACKAGE=CON7_1X7_U_2563
J4,25630401RP2,25630401RP2,CODE="NorComp 25630401RP2",EID=15,PACKAGE=CON4_1X4_U_2563
J5,25630401RP2,25630401RP2,CODE="NorComp 25630401RP2",EID=18,PACKAGE=CON4_1X4_U_2563
J6,TBLOCK-M2,TBLOCK-M2,EID=2B,PACKAGE=TBLOCK-M2
J7,25630701RP2,25630701RP2,CODE="NorComp 25630701RP2",EID=2C,PACKAGE=CON7_1X7_U_2563
J8,25630301RP2,25630301RP2,CODE="NorComp 25630301RP2",EID=33,PACKAGE=CON3_1X3_U_2563
J9,25630801RP2,25630801RP2,CODE="NorComp 25630801RP2",EID=12,PACKAGE=CON8_1X8_U_2563
J10,PIN,PIN,EID=14,PACKAGE=PIN
J11,PIN,PIN,EID=19,PACKAGE=PIN
J12,PIN,PIN,EID=34,PACKAGE=PIN
J13,PIN,PIN,EID=29,PACKAGE=PIN
J14,PIN,PIN,EID=45,PACKAGE=PIN
J15,PIN,PIN,EID=42,PACKAGE=PIN
J16,PIN,PIN,EID=49,PACKAGE=PIN
J17,PIN,PIN,EID=46,PACKAGE=PIN
J18,PIN,PIN,EID=38,PACKAGE=PIN
J19,PIN,PIN,EID=39,PACKAGE=PIN
J20,PIN,PIN,EID=3B,PACKAGE=PIN
J21,PIN,PIN,EID=3E,PACKAGE=PIN
J22,PIN,PIN,EID=43,PACKAGE=PIN
Q1,2N7002,2N7002,EID=E,L=2.5E-6,PACKAGE=SOT23,SPICELIB=SUPERTEX,SPICEMODEL=2N7002,W=0.5E-2
Q2,2N7002,2N7002,EID=10,L=2.5E-6,PACKAGE=SOT23,SPICELIB=SUPERTEX,SPICEMODEL=2N7002,W=0.5E-2
Q3,2N7002,2N7002,EID=8,L=2.5E-6,PACKAGE=SOT23,SPICELIB=SUPERTEX,SPICEMODEL=2N7002,W=0.5E-2
Q4,2N7002,2N7002,EID=D,L=2.5E-6,PACKAGE=SOT23,SPICELIB=SUPERTEX,SPICEMODEL=2N7002,W=0.5E-2
Q5,2N7002,2N7002,EID=37,L=2.5E-6,PACKAGE=SOT23,SPICELIB=SUPERTEX,SPICEMODEL=2N7002,W=0.5E-2
Q6,2N7002,2N7002,EID=36,L=2.5E-6,PACKAGE=SOT23,SPICELIB=SUPERTEX,SPICEMODEL=2N7002,W=0.5E-2
Q7,2N7002,2N7002,EID=3C,L=2.5E-6,PACKAGE=SOT23,SPICELIB=SUPERTEX,SPICEMODEL=2N7002,W=0.5E-2
Q8,2N7002,2N7002,EID=3F,L=2.5E-6,PACKAGE=SOT23,SPICELIB=SUPERTEX,SPICEMODEL=2N7002,W=0.5E-2
R1,RT0805DRD074K7L,4.70k,CODE="Digikey RT0805DRD074K7L-ND",EID=9,PACKAGE=RESC2012X50,PRIMTYPE=RESISTOR
R2,RT0805DRD074K7L,4.70k,CODE="Digikey RT0805DRD074K7L-ND",EID=A,PACKAGE=RESC2012X50,PRIMTYPE=RESISTOR
R3,RT0805DRD074K7L,4.70k,CODE="Digikey RT0805DRD074K7L-ND",EID=B,PACKAGE=RESC2012X50,PRIMTYPE=RESISTOR
R4,9C08052A1002JLHFT,10K,CODE="Digikey 311-10KADKR-ND",EID=25,PACKAGE=RESC2012X50,PRIMTYPE=RESISTOR
R5,9C08052A1002JLHFT,10K,CODE="Digikey 311-10KADKR-ND",EID=26,PACKAGE=RESC2012X50,PRIMTYPE=RESISTOR
R6,9C08052A1002JLHFT,10K,CODE="Digikey 311-10KADKR-ND",EID=27,PACKAGE=RESC2012X50,PRIMTYPE=RESISTOR
R7,9C08052A1002JLHFT,10K,CODE="Digikey 311-10KADKR-ND",EID=28,PACKAGE=RESC2012X50,PRIMTYPE=RESISTOR
R8,9C08052A1003JLHFT,100K,CODE="Digikey 311-100KATR-ND",EID=1C,PACKAGE=RESC2012X50,PRIMTYPE=RESISTOR
R9,9C08052A1003JLHFT,100K,CODE="Digikey 311-100KATR-ND",EID=1D,PACKAGE=RESC2012X50,PRIMTYPE=RESISTOR
R10,9C08052A4702JLHFT,47K,CODE="Digikey 311-47KADKR-ND",EID=6,PACKAGE=RESC2012X50,PRIMTYPE=RESISTOR
R11,9C08052A9102JLHFT,91K,CODE="Digikey 311-91KACT-ND",EID=4,PACKAGE=RESC2012X50,PRIMTYPE=RESISTOR
R12,9C08052A1003JLHFT,100K,CODE="Digikey 311-100KATR-ND",EID=F,PACKAGE=RESC2012X50,PRIMTYPE=RESISTOR
R13,9C08052A1003JLHFT,100K,CODE="Digikey 311-100KATR-ND",EID=11,PACKAGE=RESC2012X50,PRIMTYPE=RESISTOR
R14,9C08052A4702JLHFT,47K,CODE="Digikey 311-47KADKR-ND",EID=17,PACKAGE=RESC2012X50,PRIMTYPE=RESISTOR
R15,9C08052A9102JLHFT,91K,CODE="Digikey 311-91KACT-ND",EID=16,PACKAGE=RESC2012X50,PRIMTYPE=RESISTOR
R16,RT0805DRE07100RL,100,CODE="Digikey RT0805DRE07100RL-ND",EID=22,PACKAGE=RESC2012X50,PRIMTYPE=RESISTOR
R17,9C08052A4702JLHFT,47K,CODE="Digikey 311-47KADKR-ND",EID=2D,PACKAGE=RESC2012X50,PRIMTYPE=RESISTOR
R18,9C08052A9102JLHFT,91K,CODE="Digikey 311-91KACT-ND",EID=2E,PACKAGE=RESC2012X50,PRIMTYPE=RESISTOR
R19,9C08052A4702JLHFT,47K,CODE="Digikey 311-47KADKR-ND",EID=2F,PACKAGE=RESC2012X50,PRIMTYPE=RESISTOR
R20,9C08052A9102JLHFT,91K,CODE="Digikey 311-91KACT-ND",EID=30,PACKAGE=RESC2012X50,PRIMTYPE=RESISTOR
R21,9C08052A4702JLHFT,47K,CODE="Digikey 311-47KADKR-ND",EID=31,PACKAGE=RESC2012X50,PRIMTYPE=RESISTOR
R22,9C08052A9102JLHFT,91K,CODE="Digikey 311-91KACT-ND",EID=32,PACKAGE=RESC2012X50,PRIMTYPE=RESISTOR
R23,9C04021A2800FLHF3,280,CODE="Digikey 311-280LDKR-ND",EID=35,PACKAGE=RESC1005X40,PRIMTYPE=RESISTOR
R24,9C04021A2800FLHF3,280,CODE="Digikey 311-280LDKR-ND",EID=3A,PACKAGE=RESC1005X40,PRIMTYPE=RESISTOR
R25,9C04021A2800FLHF3,280,CODE="Digikey 311-280LDKR-ND",EID=3D,PACKAGE=RESC1005X40,PRIMTYPE=RESISTOR
R26,9C04021A2800FLHF3,280,CODE="Digikey 311-280LDKR-ND",EID=40,PACKAGE=RESC1005X40,PRIMTYPE=RESISTOR
U1,DRV8871,DRV8871,EID=20,PACKAGE=SOIC127P600X170-9

*NETLIST,48   
NRST,2,CLASS=SIGNAL
NRST,IT
CN7,PS,14

PB13,5,CLASS=SIGNAL
PB13,GT
COLL_OUT,LBL
R1,PS,2
J2,PS,6
CN10,PS,30

PB14,5,CLASS=SIGNAL
PB14,GT
MAX_OUT,LBL
R2,PS,2
J2,PS,4
CN10,PS,28

PB15,5,CLASS=SIGNAL
PB15,GT
MIN_OUT,LBL
R3,PS,2
J2,PS,2
CN10,PS,26

OUT_V+_SIGNAL,4,CLASS=SIGNAL
OUT_V+_SIGNAL,LBL
Q1,PS,1
Q2,PS,2
R8,PS,1

PA10,4,CLASS=SIGNAL
PA10,GT
OUT_INPUT,LBL
Q1,PS,2
CN10,PS,33

OUT_TRIG,5,CLASS=SIGNAL
OUT_TRIG,LBL
Q2,PS,1
R9,PS,1
J4,PS,2
J14,PS,1

PA8,5,CLASS=SIGNAL
PA8,GT
OUT_OUTPUT,LBL
R11,PS,2
R10,PS,1
CN10,PS,23

OUT_ECHO,4,CLASS=SIGNAL
OUT_ECHO,LBL
R10,PS,2
J4,PS,3
J15,PS,1

PB4,5,CLASS=SIGNAL
PB4,GT
KEYPAD_A,LBL
R4,PS,2
J3,PS,4
CN10,PS,27

PB5,5,CLASS=SIGNAL
PB5,GT
KEYPAD_B,LBL
R5,PS,2
J3,PS,5
CN10,PS,29

PB6,5,CLASS=SIGNAL
PB6,GT
KEYPAD_C,LBL
R6,PS,2
J3,PS,6
CN10,PS,17

PB7,5,CLASS=SIGNAL
PB7,GT
KEYPAD_D,LBL
R7,PS,2
J3,PS,7
CN7,PS,21

PA6,4,CLASS=SIGNAL
PA6,GT
MOTOR_IN1,LBL
U1,IP,3
CN10,PS,13

PA7,4,CLASS=SIGNAL
PA7,GT
MOTOR_IN2,LBL
U1,IP,2
CN10,PS,15

DRIVER_ILIM,3,CLASS=SIGNAL
DRIVER_ILIM,LBL
U1,PS,4
R16,PS,2

PC8,4,CLASS=POWER
PC8,GT
KEYPAD_3,LBL
J3,PS,1
CN10,PS,2

PC7,4,CLASS=SIGNAL
PC7,GT
KEYPAD_2,LBL
J3,PS,2
CN10,PS,19

PC6,4,CLASS=SIGNAL
PC6,GT
KEYPAD_1,LBL
J3,PS,3
CN10,PS,4

MOTOR_Q2,4,CLASS=SIGNAL
MOTOR_Q2,LBL
J7,PS,1
R21,PS,2
J22,PS,1

MOTOR_IDX,4,CLASS=SIGNAL
MOTOR_IDX,LBL
J7,PS,2
R19,PS,2
J21,PS,1

MOTOR_Q1,4,CLASS=SIGNAL
MOTOR_Q1,LBL
J7,PS,3
R17,PS,2
J20,PS,1

PC11,8,CLASS=SIGNAL
PC11,GT
MOTOR_OUT1,LBL
R17,PS,1
R18,PS,2
CN7,PS,2
U1,OP,6
J7,PS,5
J18,PS,1

PB10,8,CLASS=SIGNAL
PB10,GT
MOTOR_OUT2,LBL
R19,PS,1
R20,PS,2
CN10,PS,25
U1,OP,8
J7,PS,6
J19,PS,1

PC12,5,CLASS=SIGNAL
PC12,GT
MOTOR_OUT3,LBL
R21,PS,1
R22,PS,2
CN7,PS,3

PA11,4,CLASS=SIGNAL
PA11,GT
LCD_IN,LBL
J8,PS,2
CN10,PS,14

LED1_CONNECT2,3,CLASS=SIGNAL
LED1_CONNECT2,LBL
Q5,PS,1
J9,PS,2

PC10,4,CLASS=SIGNAL
PC10,GT
LED1_IN,LBL
Q5,PS,2
CN7,PS,1

LED1_CONNECT1,3,CLASS=SIGNAL
LED1_CONNECT1,LBL
R23,PS,1
J9,PS,1

{NC},41
CN10,PS,34
CN10,PS,24
CN10,PS,22
CN10,PS,12
CN10,PS,11
CN10,PS,6
CN10,PS,5
CN10,PS,3
CN7,PS,38
CN7,PS,37
CN7,PS,34
CN7,PS,32
CN7,PS,30
CN7,PS,28
CN10,PS,8
CN10,PS,7
CN10,PS,38
CN10,PS,37
CN10,PS,36
CN10,PS,35
CN10,PS,31
CN10,PS,18
CN10,PS,10
CN7,PS,9
CN7,PS,7
CN7,PS,6
CN7,PS,5
CN7,PS,4
CN7,PS,33
CN7,PS,31
CN7,PS,29
CN7,PS,27
CN7,PS,26
CN7,PS,25
CN7,PS,24
CN7,PS,23
CN7,PS,17
CN7,PS,15
CN7,PS,13
CN7,PS,11
CN7,PS,10

LED2_CONNECT2,3,CLASS=SIGNAL
LED2_CONNECT2,LBL
Q6,PS,1
J9,PS,4

PC1,4,CLASS=SIGNAL
PC1,GT
LED2_IN,LBL
Q6,PS,2
CN7,PS,36

LED2_CONNECT1,3,CLASS=SIGNAL
LED2_CONNECT1,LBL
R24,PS,1
J9,PS,3

LED3_CONNECT2,3,CLASS=SIGNAL
LED3_CONNECT2,LBL
Q7,PS,1
J9,PS,6

PC2,4,CLASS=SIGNAL
PC2,GT
LED3_IN,LBL
Q7,PS,2
CN7,PS,35

LED3_CONNECT1,3,CLASS=SIGNAL
LED3_CONNECT1,LBL
R25,PS,1
J9,PS,5

LED4_CONNECT2,3,CLASS=SIGNAL
LED4_CONNECT2,LBL
Q8,PS,1
J9,PS,8

PB12,4,CLASS=SIGNAL
PB12,GT
LED4_IN,LBL
Q8,PS,2
CN10,PS,16

LED4_CONNECT1,3,CLASS=SIGNAL
LED4_CONNECT1,LBL
R26,PS,1
J9,PS,7

IN_V+_SIGNAL,4,CLASS=SIGNAL
IN_V+_SIGNAL,LBL
Q3,PS,1
Q4,PS,2
R12,PS,1

PA9,4,CLASS=SIGNAL
PA9,GT
IN_INPUT,LBL
Q3,PS,2
CN10,PS,21

IN_TRIG,5,CLASS=SIGNAL
IN_TRIG,LBL
Q4,PS,1
R13,PS,1
J5,PS,2
J16,PS,1

PC9,5,CLASS=SIGNAL
PC9,GT
IN_OUTPUT,LBL
R15,PS,2
R14,PS,1
CN10,PS,1

IN_ECHO,4,CLASS=SIGNAL
IN_ECHO,LBL
R14,PS,2
J5,PS,3
J17,PS,1

+3.3V,10,CLASS=POWER
+3.3V,PR
POWER_3.3,LBL
C1,PS,2
J10,PS,1
C4,PS,2
J2,PS,5
J2,PS,3
J2,PS,1
CN7,PS,16
CN7,PS,12

+5.0V,30,CLASS=POWER
+5.0V,PR
IN_V+_POWER,LBL
IN_POWER,LBL
LED_POWER,LBL
LCD_POWER,LBL
POWER_5.0,LBL
OUT_V+_POWER,LBL
OUT_POWER,LBL
R12,PS,2
R13,PS,2
C7,PS,2
J5,PS,1
C8,PS,2
C11,PS,2
R23,PS,2
R24,PS,2
R25,PS,2
R26,PS,2
J8,PS,1
C10,PS,2
J7,PS,4
C12,PS,2
C2,PS,2
J11,PS,1
R8,PS,2
R9,PS,2
C5,PS,2
J4,PS,1
C6,PS,2
CN7,PS,18

+12.0V,9,CLASS=POWER
+12.0V,PR
POWER_12.0,LBL
MOTOR_POWER,LBL
C3,PS,2
J1,PS,2
J12,PS,1
U1,PP,5
J6,PS,2
C9,PS,2

GND,63,CLASS=POWER
GND,PR
IN_V+_GND,LBL
IN_GND,LBL
LED_GND,LBL
LCD_GND,LBL
GND_12.0,LBL
MOTOR_GND,LBL
KEYPAD_GND,LBL
GND_5.0,LBL
GND_3.3,LBL
OUT_V+_GND,LBL
OUT_GND,LBL
COLL_GND,LBL
C12,PS,1
Q3,PS,3
R15,PS,1
Q4,PS,3
C7,PS,1
C8,PS,1
J5,PS,4
Q5,PS,3
C11,PS,1
Q6,PS,3
Q7,PS,3
Q8,PS,3
J8,PS,3
C10,PS,1
J13,PS,1
J1,PS,1
C3,PS,1
U1,PP,9
U1,PP,7
J7,PS,7
R16,PS,1
U1,PP,1
J6,PS,1
C9,PS,1
R18,PS,1
R20,PS,1
R22,PS,1
R4,PS,1
R5,PS,1
R6,PS,1
R7,PS,1
C2,PS,1
C1,PS,1
Q1,PS,3
R11,PS,1
Q2,PS,3
C5,PS,1
C6,PS,1
J4,PS,4
R1,PS,1
C4,PS,1
R2,PS,1
R3,PS,1
CN10,PS,9
CN10,PS,32
CN10,PS,20
CN7,PS,8
CN7,PS,22
CN7,PS,20
CN7,PS,19

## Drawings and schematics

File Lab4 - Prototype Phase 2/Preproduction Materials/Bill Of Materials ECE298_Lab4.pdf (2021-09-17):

# Bill Of Materials for ECE298_Lab4

Design Title | ECE298_Lab4

## Author Document Number Revision

Design Created | July 30, 2021

## Design Last Modified August 1, 2021 Total Parts In Design 71

## 0Modules

Quantity | References | Value | StockCode | Unit Cost
Sub-totals: | | | | £0.00

## 12Capacitors

Quantity | References | Value | StockCode | Unit Cost
3 | C1-C3 | 10u | Digikey 478-1573-1-ND
9 | C4-C12 | 10000pF | Digikey 311-1045-2-ND
Sub-totals: | | | | £0.00

## 26Resistors

Quantity | References | Value | StockCode | Unit Cost
3 | R1-R3 | 4.70k | Digikey RT0805DRD074K7L-ND
4 | R4-R7 | 10K | Digikey 311-10KADKR-ND
4 | R8-R9,R12-R13 | 100K | Digikey 311-100KATR-ND
5 | R10,R14,R17,R19,R21 | 47K | Digikey 311-47KADKR-ND
5 | R11,R15,R18,R20,R22 | 91K | Digikey 311-91KACT-ND
1 | R16 | 100 | Digikey RT0805DRE07100RL-ND
4 | R23-R26 | 280 | Digikey 311-280LDKR-ND
Sub-totals: | | | | £0.00

## 1Integrated Circuits

Quantity | References | Value | StockCode | Unit Cost
1 | U1 | DRV8871
Sub-totals: | | | | £0.00

## 8Transistors

Quantity | References | Value | StockCode | Unit Cost
8 | Q1-Q8 | 2N7002
Sub-totals: | | | | £0.00

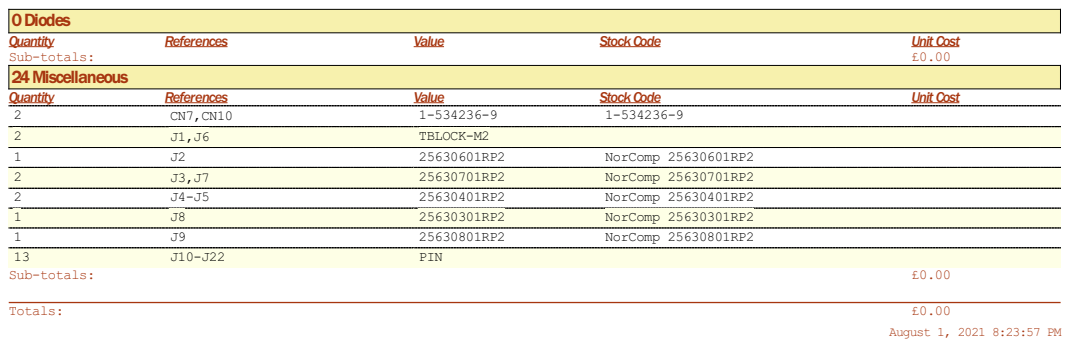
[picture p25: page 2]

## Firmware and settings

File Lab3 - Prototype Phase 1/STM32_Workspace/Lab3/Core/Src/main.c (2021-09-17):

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
/* Includes ------------------------------------------------------------------*/
#include "main.h"

/* USER CODE BEGIN Includes */
#include <stdio.h>
#include <string.h>
/* USER CODE END Includes */

TIM_HandleTypeDef htim2;
TIM_HandleTypeDef htim3;

UART_HandleTypeDef huart6;

/* USER CODE BEGIN PV */
unsigned char mode = 0; //0 for not assigned, 1 for locked, 2 for set, 3 for run
unsigned char choose_mode_flag = 0;

/*keypad related */
unsigned char keypad_sum = 0;
unsigned char keypad_val = 0;
unsigned char previous_keypad_val = 12;

/* locked mode related */
unsigned char choose_locked_flag = 0;
unsigned char choose_locked_state = 0; //0  for not assigned, 1 for fully open, 2 for fully closed
unsigned char locked_start_flag = 0;

/* set up mode related*/
unsigned char choose_setup_flag = 0;
unsigned char input_parameter_flag = 0;
unsigned char input_parameter = 0; // 0 for not assigned, 1 for outside sense distance,2 for inside
								   // 3 for remain open time, 4 for ramp up, 5 for ramp down
unsigned char input_line = 1;

unsigned char outside_sensing_distance = 4;   //setup mode default values
unsigned char inside_sensing_distance = 4;
unsigned int remain_open_time = 10;
unsigned char ramp_up_const = 5;
unsigned char ramp_down_const = 5;

/* motor related */
int motor_rvl = 0;;
unsigned int last_direction = 99;
unsigned int motor_direction = 99;
unsigned char motor_status = 0;
unsigned char outside_motor_flag = 0;
unsigned char inside_motor_flag = 0;

unsigned char start_running_flag = 0;
unsigned char start_rotating_flag = 0;
unsigned char delayed_flag = 0;

/* distance sensor related */
unsigned char ultra_direction = 2;
unsigned char outside_ultra_flag = 0;
unsigned char inside_ultra_flag = 0;
unsigned char outside_rising_flag = 1;
unsigned char inside_rising_flag = 1;

unsigned int outside_ultra_start = 0;
unsigned int outside_ultra_end = 0;
unsigned int outside_ultra_time = 0;
unsigned int outside_ultra_distance = 0;
unsigned int inside_ultra_start = 0;
unsigned int inside_ultra_end = 0;
unsigned int inside_ultra_time = 0;
unsigned int inside_ultra_distance = 0;

/* switch related */
unsigned char after_colli_flag = 0;
unsigned char min_switch_flag = 0;
unsigned char max_switch_flag = 0;
unsigned char max_motor_flag = 0;
unsigned char min_motor_flag = 0;
unsigned char colli_switch_flag = 0;
unsigned char colli_rising_flag = 1;
unsigned char colli_motor_flag = 0;



uint8_t LCD_INST = 0xFE;
uint8_t LCD_FIRST = 128;
uint8_t LCD_SECOND = 192;
uint8_t LCD_CLEAN = 1;
/* USER CODE END PV */

void SystemClock_Config(void);
static void MX_GPIO_Init(void);
static void MX_TIM2_Init(void);
static void MX_TIM3_Init(void);
static void MX_USART6_UART_Init(void);
/* USER CODE BEGIN 0 */
unsigned char get_col_val(unsigned char row_val)
{
	unsigned char col_val;
	HAL_GPIO_WritePin(GPIOC,GPIO_PIN_6|GPIO_PIN_7|GPIO_PIN_8,GPIO_PIN_RESET);
	HAL_GPIO_WritePin(GPIOC,GPIO_PIN_6,GPIO_PIN_SET);
	if(HAL_GPIO_ReadPin(GPIOB,row_val) == 1)
		col_val = 1;
	HAL_GPIO_WritePin(GPIOC,GPIO_PIN_6,GPIO_PIN_RESET);

	HAL_GPIO_WritePin(GPIOC,GPIO_PIN_7,GPIO_PIN_SET);
	if(HAL_GPIO_ReadPin(GPIOB,row_val) == 1)
		col_val = 2;
	HAL_GPIO_WritePin(GPIOC,GPIO_PIN_7,GPIO_PIN_RESET);

	HAL_GPIO_WritePin(GPIOC,GPIO_PIN_8,GPIO_PIN_SET);
	if(HAL_GPIO_ReadPin(GPIOB,row_val) == 1)
		col_val = 3;
	HAL_GPIO_WritePin(GPIOC,GPIO_PIN_8,GPIO_PIN_RESET);

	HAL_GPIO_WritePin(GPIOC,GPIO_PIN_6|GPIO_PIN_7|GPIO_PIN_8,GPIO_PIN_SET);
	return col_val;
}
unsigned char key_pressed()
{
	unsigned char col_val;
	unsigned char key_array[] = {1,2,3,4,5,6,7,8,9,10,0,11};

	if(HAL_GPIO_ReadPin(GPIOB,GPIO_PIN_4) == 1)
	{
		col_val = get_col_val(GPIO_PIN_4);
		return key_array[col_val-1];

	}
	else if(HAL_GPIO_ReadPin(GPIOB,GPIO_PIN_5) == 1)
	{
		col_val = get_col_val(GPIO_PIN_5);
		return key_array[col_val+2];

	}
	else if(HAL_GPIO_ReadPin(GPIOB,GPIO_PIN_6) == 1)
	{
		col_val = get_col_val(GPIO_PIN_6);
		return key_array[col_val+5];

	}
	else if(HAL_GPIO_ReadPin(GPIOB,GPIO_PIN_7) == 1)
	{
		col_val = get_col_val(GPIO_PIN_7);
		return key_array[col_val+8];

	}
	else
		return 12;

}

void mode_switch_reset()
{

	keypad_sum = 0;
	choose_locked_flag = 0;
	choose_locked_state = 0;
	locked_start_flag = 0;
	choose_setup_flag = 0;
	input_parameter_flag = 0;
	input_parameter = 0;

	last_direction = 99;
	motor_direction = 99;
	motor_status = 0;
	outside_motor_flag = 0;
	inside_motor_flag = 0;

	start_running_flag = 0;
	start_rotating_flag = 0;
	delayed_flag = 0;

	ultra_direction = 2;
	outside_ultra_flag = 0;
	inside_ultra_flag = 0;
	outside_rising_flag = 1;
	inside_rising_flag = 1;

	after_colli_flag = 0;
	min_switch_flag = 0;
	max_switch_flag = 0;
	max_motor_flag = 0;
	min_motor_flag = 0;
	colli_switch_flag = 0;
	colli_rising_flag = 1;
	colli_motor_flag = 0;
	outside_ultra_start = 0;
	outside_ultra_end = 0;
	outside_ultra_time = 0;
	outside_ultra_distance = 0;
	inside_ultra_start = 0;
	inside_ultra_end = 0;
	inside_ultra_time = 0;
	inside_ultra_distance = 0;

	HAL_GPIO_WritePin(GPIOC, GPIO_PIN_10|GPIO_PIN_1|GPIO_PIN_2, GPIO_PIN_RESET);
	HAL_GPIO_WritePin(GPIOB, GPIO_PIN_12, GPIO_PIN_RESET);
}

void change_line()
{
	HAL_UART_Transmit(&huart6,&LCD_INST,1,1000);
	if(input_line == 1)
	{
		HAL_UART_Transmit(&huart6,&LCD_SECOND,1,1000);
		input_line = 2;
	}
	else
	{
		HAL_UART_Transmit(&huart6,&LCD_CLEAN,1,1000);
		HAL_UART_Transmit(&huart6,&LCD_FIRST,1,1000);
		input_line = 1;
	}
	 HAL_Delay(10);
}

void clean_LCD()
{
	HAL_UART_Transmit(&huart6,&LCD_INST,1,1000);
	HAL_UART_Transmit(&huart6,&LCD_CLEAN,1,1000);
	input_line = 1;
	HAL_Delay(10);
}

void display_mode()
{
	if(mode == 2)
	{
		clean_LCD();
		uint8_t buff_setup[] = "Setup";
		HAL_UART_Transmit(&huart6, buff_setup, sizeof(buff_setup), 1000);
		change_line();
	}
	else if(mode == 3)
	{
		clean_LCD();
		uint8_t buff_run[] = "Run";
		HAL_UART_Transmit(&huart6, buff_run, sizeof(buff_run), 1000);
		change_line();
	}
}

void choose_mode()
{
	char buff[100];
	if((keypad_val == 1||keypad_val == 2||keypad_val == 3) && keypad_val != previous_keypad_val)
	{
		keypad_sum = keypad_val;
		previous_keypad_val = keypad_val;
		snprintf(buff, 100, "%d", keypad_val);
		HAL_UART_Transmit(&huart6, (uint8_t*)buff, strlen(buff), 1000);

	}
	else if(keypad_val == 11 && keypad_val != previous_keypad_val)
	{
		previous_keypad_val = keypad_val;
		mode = keypad_sum;
		choose_mode_flag = 0;
		mode_switch_reset();


	}
}

void choose_setup()
{
	char buff[100];


	if(keypad_val <=5 && keypad_val >=1 && keypad_val != previous_keypad_val)
	{
		keypad_sum = keypad_val;
		previous_keypad_val = keypad_val;
		snprintf(buff, 100, "%d", keypad_sum);
		HAL_UART_Transmit(&huart6, (uint8_t*)buff, strlen(buff), 1000);
	}
	else if(keypad_val == 11 && keypad_val!=previous_keypad_val)
	{
		previous_keypad_val = keypad_val;
		input_parameter = keypad_sum;
		choose_setup_flag = 0;
		keypad_sum = 0;
		input_parameter_flag = 1;
		display_mode();
		snprintf(buff, 100, "%s%d %s","P" ,input_parameter,"Value: ");
		HAL_UART_Transmit(&huart6,(uint8_t*)buff, strlen(buff), 1000);
	}
}

void get_parameter()
{
	char buff[100];
	uint8_t buff_setup_start[] = "PARAMETER NO.:";
	uint8_t buff_error[] = "WRONG VALUE";
	if(keypad_val != previous_keypad_val)
	{
		previous_keypad_val = keypad_val;
		if(keypad_val <= 9)
		{
		keypad_sum = keypad_sum*10 + keypad_val;
		snprintf(buff, 100, "%d", keypad_val);
		HAL_UART_Transmit(&huart6, (uint8_t*)buff, strlen(buff), 1000);
		}
		else if(keypad_val == 11)
		{
			if(input_parameter == 1||input_parameter == 2)
			{
				if(keypad_sum == 2||keypad_sum ==4||keypad_sum ==6||keypad_sum ==8)
				{
					if(input_parameter == 1)
						outside_sensing_distance = keypad_sum;
					else
						inside_sensing_distance = keypad_sum;
					display_mode();
					HAL_UART_Transmit(&huart6, buff_setup_start, sizeof(buff_setup_start), 1000);
					keypad_sum = 0;
					input_parameter_flag = 0;
					choose_setup_flag = 1;
				}
				else
				{
					display_mode();
					HAL_UART_Transmit(&huart6,buff_error, sizeof(buff_error), 1000);
					HAL_Delay(100);
					display_mode();
					snprintf(buff, 100, "%s%d %s","P" ,input_parameter,"Value: ");
					HAL_UART_Transmit(&huart6,(uint8_t*)buff, strlen(buff), 1000);
					keypad_sum = 0;
				}
			}


			else if(input_parameter ==3)
			{
				if(keypad_sum == 5||keypad_sum ==10||keypad_sum ==15||keypad_sum ==20)
				{
					remain_open_time = keypad_sum;
					keypad_sum = 0;
					display_mode();
					HAL_UART_Transmit(&huart6, buff_setup_start, sizeof(buff_setup_start), 1000);
					input_parameter_flag = 0;
					choose_setup_flag = 1;

				}
				else
				{
					display_mode();
					HAL_UART_Transmit(&huart6,buff_error, sizeof(buff_error), 1000);
					HAL_Delay(100);
					display_mode();
					snprintf(buff, 100, "%s%d %s","P" ,input_parameter,"Value: ");
					HAL_UART_Transmit(&huart6,(uint8_t*)buff, strlen(buff), 1000);
					keypad_sum = 0;
				}

			}
			else if(input_parameter == 4 ||input_parameter == 5)
			{
				if(keypad_sum >= 1 && keypad_sum <= 9)
				{

					if(input_parameter == 4)
						ramp_up_const = keypad_sum;
					else
						ramp_down_const = keypad_sum;
					keypad_sum = 0;
					display_mode();
					HAL_UART_Transmit(&huart6, buff_setup_start, sizeof(buff_setup_start), 1000);
					input_parameter_flag = 0;
					choose_setup_flag = 1;

				}
				else
				{
					display_mode();
					HAL_UART_Transmit(&huart6,buff_error, sizeof(buff_error), 1000);
					HAL_Delay(100);
					display_mode();
					snprintf(buff, 100, "%s%d %s","P" ,input_parameter,"Value: ");
					HAL_UART_Transmit(&huart6,(uint8_t*)buff, strlen(buff), 1000);
					keypad_sum = 0;
				}

			}

		}
	}

}

void check_limit_min()
{

	if(min_switch_flag)
	{
		uint8_t buff_min[] = "DETECT MIN LIMIT";
		display_mode();
		HAL_UART_Transmit(&huart6,buff_min, sizeof(buff_min), 1000);
		min_switch_flag = 0;
		min_motor_flag=1;
	}
}
void check_limit_max()
{
	if(max_switch_flag)
	{
		uint8_t buff_max[] = "DETECT MAX LIMIT";
		display_mode();
		HAL_UART_Transmit(&huart6,buff_max, sizeof(buff_max), 1000);
		max_switch_flag = 0;
		max_motor_flag = 1;
	}
}
void check_collision()
{

	if(colli_switch_flag)
	{
		uint8_t buff_colli[] = "DETECT COLLISION";
		display_mode();
		if(colli_rising_flag)
		{
			HAL_UART_Transmit(&huart6,buff_colli, sizeof(buff_colli), 1000);
			colli_rising_flag = 0;
			colli_motor_flag = 1;
		}
		else

		{
			HAL_GPIO_WritePin(GPIOC, GPIO_PIN_2, GPIO_PIN_RESET);
			colli_rising_flag = 1;
		}
		colli_switch_flag = 0;
	}
}
void check_ultra_out()
{
	uint8_t buff_outside[] = "DETECT OUTSIDE";
	if(outside_ultra_flag == 1)
	{
		display_mode();
		HAL_UART_Transmit(&huart6,buff_outside, sizeof(buff_outside), 1000);
		HAL_GPIO_WritePin(GPIOC, GPIO_PIN_10, GPIO_PIN_SET);
		outside_ultra_flag = 0;
	}
	else if(outside_ultra_flag == 2)
	{
		HAL_GPIO_WritePin(GPIOC, GPIO_PIN_10, GPIO_PIN_RESET);
		display_mode();
		outside_ultra_flag = 0;
	}
}
void check_ultra_in()
{
	uint8_t buff_inside[] = "DETECT INSIDE";
	if(inside_ultra_flag == 1)
	{
		display_mode();
		HAL_UART_Transmit(&huart6,buff_inside, sizeof(buff_inside), 1000);
		HAL_GPIO_WritePin(GPIOC, GPIO_PIN_1, GPIO_PIN_SET);
		inside_ultra_flag = 0;
	}
	else if(inside_ultra_flag == 2)
	{
		HAL_GPIO_WritePin(GPIOC, GPIO_PIN_1, GPIO_PIN_RESET);
		inside_ultra_flag = 0;
		if(outside_ultra_flag != 1)
			display_mode();

	}
}


void accle(uint32_t value)
{
	TIM3->CCR1 = value*160;
	TIM3->CCR2 = 0;
}

void deccle(uint8_t value)
{
	TIM3->CCR2 = value*160;
	TIM3->CCR1 = 0;
}
void quick_accle()
{
	TIM3->CCR1 = 1599;
	TIM3->CCR2 = 0;
}
void quick_deccle()
{
	TIM3->CCR2 = 1599;
	TIM3->CCR1 = 0;
}

void clk_rotate()
{
	  if(motor_rvl >= 11 ||(start_rotating_flag && max_motor_flag)||(start_rotating_flag && colli_motor_flag))
	  {
		  if(mode == 1)
			  deccle(3);
		  if(mode == 3 && !after_colli_flag)
			  deccle(ramp_down_const/2+1);
		  if(mode == 3 && after_colli_flag)
			  deccle(2);
	  }
	  else
	  {
		  if(mode == 1)
			  accle(5);
		  if(mode == 3 && !after_colli_flag)
			  accle(ramp_up_const);
		  if(mode == 3 && after_colli_flag)
			  accle(3);

	  }
}
void counter_clk_rotate()
{
	  if(motor_rvl <= 0||(start_rotating_flag && min_motor_flag)||(start_rotating_flag && colli_motor_flag))
	  {
		  if(mode == 1)
			  accle(3);
		  if(mode == 3 && !after_colli_flag)
			  accle(ramp_up_const/2+1);
		  if(mode == 1 && after_colli_flag)
		  	  accle(2);
	  }
	  else
	  {
		  if(mode == 1)
			  deccle(5);
		  if(mode == 3 && !after_colli_flag)
			  deccle(ramp_down_const);
		  if(mode == 3 && after_colli_flag)
			  deccle(3);
	  }
}
void no_rotate()
{
	  last_direction = 99;
	  motor_direction = 99;
	  accle(0);
	  deccle(0);
}
/* USER CODE END 0 */

/**
  * @brief  The application entry point.
  * @retval int
  */
int main(void)
{
  /* USER CODE BEGIN 1 */
  uint8_t buff_mode_select[] = "MODE SELECT:";
  uint8_t buff_locked_select[] = "PRESS SWITCH:";
  uint8_t buff_locked_open[] = "FULLY OPEN";
  uint8_t buff_locked_closed[] = "FULLY CLOSED";
  uint8_t buff_setup_start[] = "PARAMETER NO.:";
  motor_rvl=0;
  /* USER CODE END 1 */

  /* MCU Configuration--------------------------------------------------------*/

  /* Reset of all peripherals, Initializes the Flash interface and the Systick. */
  HAL_Init();

  /* Configure the system clock */
  SystemClock_Config();

  /* Initialize all configured peripherals */
  MX_GPIO_Init();
  MX_TIM2_Init();
  MX_TIM3_Init();
  MX_USART6_UART_Init();
  /* USER CODE BEGIN 2 */
  HAL_TIM_Base_Start(&htim3);
  HAL_TIM_PWM_Start(&htim3, TIM_CHANNEL_1);
  HAL_TIM_PWM_Start(&htim3, TIM_CHANNEL_2);
  HAL_GPIO_WritePin(GPIOB,GPIO_PIN_4|GPIO_PIN_5|GPIO_PIN_6|GPIO_PIN_7,GPIO_PIN_RESET);
  HAL_GPIO_WritePin(GPIOC,GPIO_PIN_6|GPIO_PIN_7|GPIO_PIN_8,GPIO_PIN_SET);
  HAL_TIM_Base_Start(&htim2);

  HAL_Delay(500);
  /* USER CODE END 2 */

  /* Infinite loop */
  /* USER CODE BEGIN WHILE */
  while (1)
  {

	  keypad_val = key_pressed();
	  /* choose mode start */
	  if((mode == 0 ||keypad_val == 10)&&!choose_mode_flag)
	  {
		  clean_LCD();
		  HAL_UART_Transmit(&huart6, buff_mode_select, sizeof(buff_mode_select), 1000);
		  choose_mode_flag = 1;
	  }
	  if(choose_mode_flag)
	  {
		  choose_mode();
	  }

	  /* locked mode start */
	  if(mode == 1 && !choose_locked_state && !choose_locked_flag &&!choose_mode_flag) //locked
	  {
		  choose_locked_flag = 1;
		  clean_LCD();
		  HAL_UART_Transmit(&huart6,buff_locked_select, sizeof(buff_locked_select), 1000);
	  }
	  if(mode == 1 && choose_locked_state == 1 && !locked_start_flag && !choose_mode_flag)
	  {
		  change_line();
		  HAL_UART_Transmit(&huart6,buff_locked_open, sizeof(buff_locked_open), 1000);
		  locked_start_flag = 1;
		  motor_status = 1;

	  }
	  if(mode == 1 && choose_locked_state==2 && !locked_start_flag &&!choose_mode_flag)
	  {
		  change_line();
		  HAL_UART_Transmit(&huart6,buff_locked_closed, sizeof(buff_locked_closed), 1000);
		  locked_start_flag = 1;
		  motor_status = 2;

	  }
	  if(mode ==1 && motor_status ==1 && locked_start_flag && !choose_mode_flag)
	  {
		  if(motor_rvl == 11)
		  	  motor_status = 0;
		  else
			  clk_rotate();
	  }
	  if(mode ==1 && motor_status ==2 && locked_start_flag && !choose_mode_flag)
	  {
		 if(motor_rvl == 0)
			  motor_status = 0;
		 else
		 	 counter_clk_rotate();
	  }

	  if(mode ==1 && motor_status ==0 && locked_start_flag && !choose_mode_flag)
	  {
		  no_rotate();

	  }

	  /* set mode start */
	  if(mode ==2 && !choose_setup_flag &&!input_parameter_flag &&!choose_mode_flag)
	  {
		  display_mode();
		  HAL_UART_Transmit(&huart6, buff_setup_start, sizeof(buff_setup_start), 1000);
		  choose_setup_flag = 1;
	  }

	  if(mode ==2 && choose_setup_flag &&!choose_mode_flag)
	  {
		  choose_setup();
	  }
	  if(mode ==2 && input_parameter_flag &&!choose_mode_flag)
	  {
		  get_parameter();
	  }

	  /* run mode start */
	  if(mode ==3 &&!choose_mode_flag &&!start_running_flag)
	  {
		  display_mode();
		  start_running_flag = 1;
	  }
	  if(start_running_flag && !choose_mode_flag)
	  {
		  check_ultra_out();
		  check_ultra_in();
		  check_limit_min();
		  check_limit_max();
		  check_collision();
	  }
	  if(start_running_flag && !choose_mode_flag && (outside_motor_flag == 1||inside_motor_flag == 1) && !start_rotating_flag)
	  {
		  motor_status = 1;
		  outside_motor_flag = 0;
		  inside_motor_flag = 0;
		  start_rotating_flag = 1;
	  }

	  if(mode == 3 && motor_status == 1 && !choose_mode_flag && start_rotating_flag)
	  {
		  clk_rotate();
	  }

	  if(mode ==3 && motor_status ==2 &&!choose_mode_flag && start_rotating_flag)
	  {
		  counter_clk_rotate();
		  if(outside_motor_flag == 1||inside_motor_flag == 1)
		  {
			  motor_status = 1;
			  outside_motor_flag = 0;
			  inside_motor_flag = 0;
		  }
	  }

	  if(mode == 3 && motor_status == 0 && !choose_mode_flag && start_rotating_flag)
	  {
		  if(ultra_direction == 2)
			  ultra_direction = motor_direction;

		  if(ultra_direction == 0)
		  {
			  no_rotate();
			  if(!colli_motor_flag)
			  {
				  if(max_motor_flag)
					  motor_rvl = 11;
				  if(!delayed_flag)
				  {
					  HAL_Delay(100*remain_open_time);
					  //delay_ms(remain_open_time*1000);
					  delayed_flag = 1;
				  }
				  if(outside_motor_flag == 2 && inside_motor_flag == 2)
				  {
					  motor_status = 2;
					  delayed_flag = 0;
					  outside_motor_flag = 0;
					  inside_motor_flag = 0;
					  ultra_direction = 2;
				  }
			  }
			  else
			  {
				  if(colli_rising_flag)
				  {
					  colli_motor_flag = 0;
					  motor_status = 1;
					  ultra_direction = 2;
					  after_colli_flag = 1;
				  }
			  }
		  }

		  else if(ultra_direction == 1)
		  {
			  no_rotate();
			  if(!colli_motor_flag)
			  {
				  if(min_motor_flag)
					motor_rvl = 0;
				  start_rotating_flag = 0;
				  ultra_direction = 2;
				  after_colli_flag = 0;
			  }
			  else
			  {
				  if(colli_rising_flag)
				  {
					  colli_motor_flag = 0;
					  motor_status = 2;
					  ultra_direction = 2;
					  after_colli_flag = 1;
				  }
			  }
		  }
		  max_motor_flag = 0;
		  min_motor_flag = 0;

	  }
	  if(mode == 3 && colli_motor_flag && !choose_mode_flag && start_rotating_flag)
	  {
		  HAL_GPIO_TogglePin(GPIOC,GPIO_PIN_2);
	  }
	  else
	  {
		  HAL_GPIO_WritePin(GPIOC,GPIO_PIN_2,GPIO_PIN_RESET);
	  }
	  if(mode == 3 && !colli_motor_flag && !choose_mode_flag && start_rotating_flag && motor_status != 0)
	  {
		  HAL_GPIO_TogglePin(GPIOB,GPIO_PIN_12);
	  }
	  else
	  {
		  HAL_GPIO_WritePin(GPIOB,GPIO_PIN_12,GPIO_PIN_RESET);
	  }

	  /* distance sensor trigger */
	  HAL_GPIO_TogglePin(GPIOA,GPIO_PIN_9);
	  HAL_GPIO_TogglePin(GPIOA,GPIO_PIN_10);
	  HAL_Delay(100);
    /* USER CODE END WHILE */

    /* USER CODE BEGIN 3 */
  }
  /* USER CODE END 3 */
}

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
/* USER CODE BEGIN 4 */
void HAL_GPIO_EXTI_Callback(uint16_t GPIO_Pin)
{
	if(GPIO_Pin == GPIO_PIN_8)
	{

		if(mode == 3)
		{
			if(outside_rising_flag)
			{
				outside_ultra_start = __HAL_TIM_GetCounter(&htim2);
				outside_rising_flag = 0;


			}
			else
			{
				outside_ultra_end = __HAL_TIM_GetCounter(&htim2);
				outside_rising_flag = 1;
				outside_ultra_time = outside_ultra_end - outside_ultra_start;
				outside_ultra_distance = 3.44*outside_ultra_time/2;
				if(outside_ultra_distance <= outside_sensing_distance*30.48)
				{
					outside_ultra_flag = 1;
					if(outside_motor_flag != 1){
						outside_motor_flag = 1;
					}
				}
				else
				{
					outside_ultra_flag = 2;
					if(outside_motor_flag != 2)
						outside_motor_flag = 2;
				}

			}

		}
	}
	if(GPIO_Pin == GPIO_PIN_9)
	{

		if(mode ==3)
		{

			if(inside_rising_flag)
			{
				inside_ultra_start = __HAL_TIM_GetCounter(&htim2);
				inside_rising_flag = 0;


			}
			else
			{
				inside_ultra_end = __HAL_TIM_GetCounter(&htim2);
				inside_rising_flag = 1;
				inside_ultra_time = inside_ultra_end - inside_ultra_start;
				inside_ultra_distance = 3.44*inside_ultra_time/2;
				if(inside_ultra_distance <= inside_sensing_distance*30.48)
				{
					inside_ultra_flag = 1;
					if(inside_motor_flag != 1)
						inside_motor_flag = 1;

				}
				else
				{
					inside_ultra_flag =2;
					if(inside_motor_flag != 2)
						inside_motor_flag =2;
				}


			}

		}
	}
	if(GPIO_Pin == GPIO_PIN_14)  //max_limit
	{
		if(mode ==1 && choose_locked_flag ==1) //ASSUME START OPEN, CAN BE OPTTIMIZED
		{
			choose_locked_state=1;
			choose_locked_flag=0;
		}
		else if(mode == 3)
		{
			max_switch_flag=1;
		}
	}
	if(GPIO_Pin == GPIO_PIN_15) //min_limit
	{
		if(mode ==1 && choose_locked_flag ==1)
		{
			choose_locked_state = 2;
			choose_locked_flag = 0;
		}
		else if(mode == 3)
		{
			min_switch_flag = 1;
		}
	}
	if(GPIO_Pin == GPIO_PIN_13)
	{
		if(mode == 3)
		{
			colli_switch_flag = 1;
		}
	}
	if(GPIO_Pin == GPIO_PIN_10)
	{
		if(motor_direction)
		{
		    motor_rvl += 1;
		}
		else
		{
			motor_rvl -= 1;
		}
	}

	if(GPIO_Pin == GPIO_PIN_12)
	{
		motor_direction = HAL_GPIO_ReadPin(GPIOC,GPIO_PIN_11);

		if(last_direction == 99)
		{
			last_direction = motor_direction;
		}
		if(motor_direction != last_direction)
		{
			motor_status = 0;
			//if(mode == 1)
			//	locked_start_flag = 2;
		}
	}


}
/* USER CODE END 4 */
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


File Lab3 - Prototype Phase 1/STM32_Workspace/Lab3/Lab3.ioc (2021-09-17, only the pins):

Mcu.UserName=STM32F401RETx
PC10.Signal=GPIO_Output
PC12.Signal=GPXTI12
PA14.GPIO_Label=TCK
PB13.Signal=GPXTI13
PB15.Signal=GPXTI15
PA12.Signal=USART6_RX
PB6.Signal=GPIO_Output
PC7.Signal=GPIO_Output
PB7.Signal=GPIO_Output
PA8.Signal=GPXTI8
PA6.Signal=S_TIM3_CH1
PA10.Signal=GPIO_Output
PA15.Signal=S_TIM2_CH1_ETR
PB4.Signal=GPIO_Output
PB3.GPIO_Label=SWO
PC11.Signal=GPIO_Input
PC8.Signal=GPIO_Output
PC2.Signal=GPIO_Output
PC6.Signal=GPIO_Output
PC14-OSC32_IN.Signal=RCC_OSC32_IN
PA13.Signal=SYS_JTMS-SWDIO
PA9.Signal=GPIO_Output
PC15-OSC32_OUT.Signal=RCC_OSC32_OUT
PB10.Signal=GPXTI10
PB14.Signal=GPXTI14
PA13.GPIO_Label=TMS
PB3.Signal=SYS_JTDO-SWO
PB5.Signal=GPIO_Output
PA11.Signal=USART6_TX
PA14.Signal=SYS_JTCK-SWCLK
PC9.Signal=GPXTI9
PC1.Signal=GPIO_Output
PB12.Signal=GPIO_Output
PA7.Signal=S_TIM3_CH2

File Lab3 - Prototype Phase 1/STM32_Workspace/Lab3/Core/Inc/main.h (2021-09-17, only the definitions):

#define TMS_Pin GPIO_PIN_13
#define TMS_GPIO_Port GPIOA
#define TCK_Pin GPIO_PIN_14
#define TCK_GPIO_Port GPIOA
#define SWO_Pin GPIO_PIN_3
#define SWO_GPIO_Port GPIOB

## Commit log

2021-09-17 Upload project files
    [ECE298_Lab4 - CADCAM Bottom Assembly.GBR, ECE298_Lab4 - CADCAM Bottom Copper.GBR, ECE298_Lab4 - CADCAM Bottom SMT Paste.GBR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]
2021-09-17 Update directory names
    [ECE298_Lab4 - CADCAM Bottom Assembly.GBR, ECE298_Lab4 - CADCAM Bottom Copper.GBR, ECE298_Lab4 - CADCAM Bottom SMT Paste.GBR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]

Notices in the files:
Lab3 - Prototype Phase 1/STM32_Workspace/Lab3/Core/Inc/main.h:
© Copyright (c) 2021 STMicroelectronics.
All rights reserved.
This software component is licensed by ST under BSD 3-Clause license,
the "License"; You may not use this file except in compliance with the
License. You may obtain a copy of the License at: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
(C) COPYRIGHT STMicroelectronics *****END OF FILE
